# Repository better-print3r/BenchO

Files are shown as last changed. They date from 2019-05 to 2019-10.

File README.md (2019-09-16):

# BenchO

## A universal test standard for 3D printers.



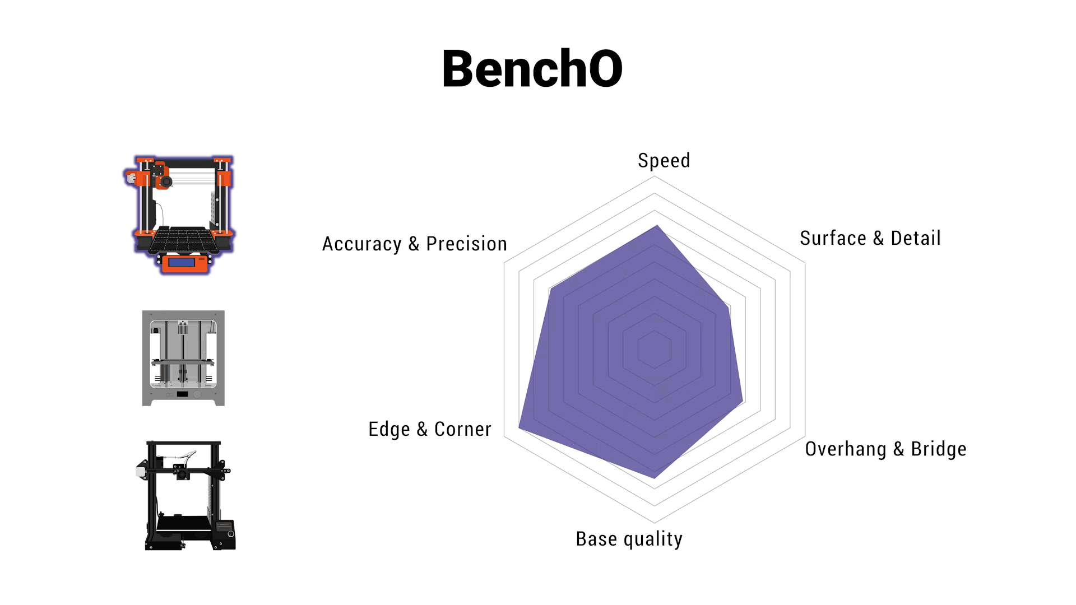
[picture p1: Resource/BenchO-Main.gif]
avatar

- #### Comprehensive
- #### Practical
- #### Professional 
## Aims of BenchO
- #### To test and compare the performance of various 3D printers
- #### To discuss and optimize profiles for different situation
- #### To calibrate and improve your printers
- #### To improve 3D printing experience for everyone
## Table of Contents
#### BenchO in a nutshell
- [What is BenchO?](#what-is-bencho)
- [Why we do this?](#why-we-do-this)
- [How do we achieve our goal?](#how-do-we-achieve-our-goal)
#### Test with BenchO
- [Preparation](#preparation)
- [Standard Test](#standard-fdm-test)
- [FAQs](#faqs)
- [Contributing](#contributing)
- [License](#license)
#### How to reach us
- [Contact infomation](#contact-infomation)

### What is BenchO?
BenchO is an open source project started by **Better Printer Institution LLC**.  Aiming to provide a universal test standard for the industry.  In our test, we provide specialized models and procedure to estimate the capability of your 3D printer.We will also provide optimized profile(in slicing software) for makers all over the world to suit thier needs. 

The current version contains protocols for consumer grade FDM printer. More test protocols will be added later in the future. The project is entirely open source.

In summary this is a place to **test, evaluate**,**discuss** and **improve** your 3D printer.

### Why we do this?

There are many 3D printers in the market and they are in all kinds of shapes and structures. For users it is really difficult to tell how much the difference really is between them.

How is the actual performance compare to what they advertised? Where is the limit of your printer? These questions are usually hard to find out.Besides that, even if you tried to find those answers, there is no such thing as a universal benchmark for you to discuss and compare with other machines. 

Thus we decide to make a universal, data based, open sourced project as you seen here. 

We believe that by making a universal standard for 3D printers, we could make this field better in the future.

### How do we achieve our goal?

In this project we currently provide a sufficient offline tool. This tool will allow 3D printer users get to know the capabilities of their machines and thus improve the performance of their printers. Our current test will be the starting point of BenchO.

## Standard FDM test

### Preparation for FDM 3D printer

- **eSUN PLA+ filament (Grey)** as standard test filament
- The 3D printer you want to test with
- A caliper with resolution up to 0.01mm and range larger than 100mm
- [BenchO Tool]() ([Offline version](Standard%20FDM%20test/BenchO_offline_ver20190902.xlsx))
- [Test Models](3Dmodel)

####
Check **[here](Standard%20FDM%20test)** to participate in BenchO test.

## FAQs
- **Q**: Why eSUN PLA+ with Grey color?
- **A**: eSUN filament is widely available all across the world. This makes BenchO testers having same material so the result is comparable. Grey is for checking surface details. We found this color be good to spot defects in your art print.
####
- **Q**:I saw the project is started by Better Printer Institution LLC. But why are you guys making profiles and improvements even for your competitors?
- **A**:Because we want a better community overall. Moderate competition and more cooperation will greatly improve the quality of 3D printing communities.This will eventually benefit us all,both users and companies.
## Maintainers

BenchO Team

## Contributing

See [the contributing file](CONTRIBUTING.md)!

Small note: If editing the Readme, please conform to the [standard-readme](https://github.com/RichardLitt/standard-readme) specification.

## License
This project is licensed under the Apache License, Version 2.0. See
[LICENSE](LICENSE)
## Contact Infomation
- The offical website:[http://foldy3d.com/](http://foldy3d.com/) 
- The Facebook Page:[https://www.facebook.com/BetterPrint3r/](https://www.facebook.com/BetterPrint3r/)

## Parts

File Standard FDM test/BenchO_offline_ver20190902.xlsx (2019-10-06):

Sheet: Basic
An Universal 3D printer test standard
Part1: Basic Precision
Section 1
Large Scale
No. | Value(mm) | Average(mm) | This part will reflect the relative precision and the absolute accuracy of your printer.The International Tolerance table reference ISO 286 has been applied here.
L1 | 99.71 | 99.55
L2 | 99.51
L3 | 99.52
L4 | 99.59 |  | For this section , all data should be enter in exact order.
L5 | 99.61
L6 | 99.47
L7 | 99.42
L8 | 99.54
 |  |  | Subject | Score | Hint:All good
 |  |  | XY relative precision | 5.48 out of 6
 |  |  | XY accuracy | 2 out of 4
 |  |  | Tolerance Grade | IT12
Section 2
Small Scale
No. | Value(mm) | Average(mm) | This part will reflect the absolute accuracy of your printer.The International Tolerance table reference ISO 286 has been applied here.
1 | 9.91 | 9.89
2 | 9.90
3 | 9.86
4 | 9.86 |  | In this section no specific data order is required.You should take data from different locations on model and fill all the blank.
5 | 9.89
6 | 9.87
7 | 9.93
8 | 9.93
9 | 9.89
10 | 9.86
Z axis
No. | Value(mm) | Average(mm) | Subject | Score | Grade | To see more details about grade, check Misc tab
1 | 100.22 | 100.27 | Small Scale accuracy | 2.8 out of 4 | IT11
2 | 100.25
3 | 100.29 |  | Z axis accuracy | 2.8 out of 4 | IT11
4 | 100.30
End of the section, please proceed to the next tab

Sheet: Engineering
BenchoO
An Universal 3D printer test standard
Part2: Engineering
Section 1
Base Quality
No. | Thickness(mm) | Average(mm) | Print Time |  | Hint:You must use your actual print time.
T1 | 9.86 | 9.94 | Hour | Min
T2 | 10.01 |  | 5 | 58
T3 | 9.77 |  | For this section , all data should be enter in exact order. This part measures the degree of parallel between base and surface.
T4 | 10.03
T5 | 9.87
T6 | 10.02
T7 | 9.80
T8 | 9.91
T9 | 10.21
Edge & Corner
No. | Thickness(mm) | Distortion(mm) | Score | Grade | This part measures the overshoot around corner.
V1 | 7.96 | 0.14 | 4.5 out of 5 | IT9
V2 | 7.91
V3 | 7.84
V4 | 7.94
V5 | 7.82
V6 | 7.83
Parallel
Feature |  | Status | Divergence(Deg) |  | Score(%) | 98.00%
Ueven X axi |  | No | 0.00955
Ueven Y axi |  | No | 0.01910
Flatness
Feature |  | Status | Score(%) | 46.00%
Uneven thickness |  | Yes
Convex |  | Yes
Section 2
Curvature
 | Bending Distance(mm)
No. | X axi
1 | 0.20
2 | 0.20
3 | 0.02
4 | 0.20
No. | Y axi
1 | 0.10
2 | 0.10
3 | 0.10
4 | 0.00
Concave Down？ |  | No
Direction |  | Radius | Score |  | The radius here refer to the circle you need if you use your base as an arc.
X axi |  | 32258.10 | 100.00%
Y axi |  | 30826.69 | 100.00%
Summary
Condition |  | Sub Total(%) | Overall(%) | Score | Hint: Even one small drawbacks can lower your score significantly
Parallel |  | 98.00% | 45.00% | 4.5 out of 10
Flatness |  | 46.00%
Curvature |  | 100.00%
Section 3
Print Time |  | Hour | Min | Hint:You must use your actual print time.
 |  | 2 | 0
Large Holes
No. | Inner(mm) | Average(mm) | Under size? |  | Hint:Precision indicates how homogeneous your circle is. While Accuracy shows how much your circle deviates from design
1 | 79.86 | 79.86 | Yes
2 | 79.87 |  | Off Set(mm)
3 | 79.82 |  | -0.18
4 | 79.91 |  | Score(%) |  | Grade | Score
5 | 79.84 |  | Precision | 60.00% | 9 | 1.3 out of 2.5
6 | 79.88 |  | Accuracy | 40.00% | IT10
Large Shafts
No. | Outer(mm) | Average(mm) | Over size? |  | Hint:Here the precision uses chart ISO 286-2,while accuracy uses chart ISO 286. To see details please check Misc tab
1 | 99.92 | 99.93 | No
2 | 99.96 |  | Off Set(mm)
3 | 99.95 |  | -0.11
4 | 99.89 |  | Score(%) |  | Grade | Score
5 | 99.90 |  | Precision | 70.00% | 8 | 1.95 out of 2.5
6 | 99.97 |  | Accuracy | 90.00% | IT9
Small Holes
No. | Inner(mm) | Average(mm) | Under size? |  | If your printer score badly this part. Dont worry. Most printers wont score over 50%
1 | 29.93 | 29.93 | Yes
2 | 29.95 |  | Off Set(mm)
3 | 29.92 |  | -0.13
4 | 29.87 |  | Score(%) |  | Grade | Score
5 | 29.93 |  | Precision | 40.00% | 10 | 1 out of 2.5
6 | 29.97 |  | Accuracy | 40.00% | IT10
Small Shafts
No. | Outer(mm) | Average(mm) | Over size? |  | Only when a hole is not under size and a shaft is not over size. It can be granted H/h grade
1 | 49.98 | 49.94 | No
2 | 49.91 |  | Off Set(mm)
3 | 49.96 |  | -0.09
4 | 49.92 |  | Score(%) |  | Grade | Score
5 | 49.94 |  | Precision | 60.00% | 9 | 1.8 out of 2.5
6 | 49.95 |  | Accuracy | 90.00% | IT9
End of the section, please proceed to the next tab

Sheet: Art
BenchoO
An Universal 3D printer test standard
Part3: Art
Section 1
Art1
Print Time |  | Hour | Min | Hint:You must use your actual print time.
 |  | 1 | 8
Subject | Condition | Score
Overhang Level | 4 | 4 out of 4
cameo level | 3 | 2.4 out of 4
Ringing size(Included) | 4mm | 3.5 out of 5
Art2
Print Time |  | Hour | Min | Hint:You must use your actual print time.
 |  | 0 | 49
Subject | Condition | Score
Clear space between bridge | Yes | 1 out of 1
Bridge to bottom Distance(mm) | 11.42 | 2.86 out of 3
Stringing | Clean | 3 out of 3
Full hieght | Yes | 1 out of 1
Disk(Minimum layer height) | 0.05mm | 2.8 out of 4
Sum | 20.56 out of 25
End of the Test. Please check Result Tab for detailed summary

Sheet: Result
BenchoO
An Universal 3D printer test standard
Result
Basic Precision
Subject | Score | Score(%) | Sum |  | Score | Score(%)
XY relative precision | 3.66 out of 4 | 91.40% |  |  | 13.08 out of 18 | 72.69%
XY accuracy | 3 out of 6 | 50.00%
Small Scale accuracy | 2.8 out of 4 | 70.00%
Z axis accuracy | 2.8 out of 4 | 70.00%
Engineering
Subject | sub Score(%) | Sub total(%) | Sub Score | Sum | Score | Score(%)
Surface Flatness | 46.00% | 45.00% | 4.5 out of 10 |  | 15.05 out of 25 | 60.20%
Surface Parallel | 98.00%
Surface Curvature | 100.00%
Subject | Score | Score(%)
Vertical Distortion | 4.5 out of 5 | 90.00%
Shafts | 3.75 out of 5 | 75.00%
Holes | 2.3 out of 5 | 46.00%
Art
Surface condition |  |  |  | Sum | Score | Score(%)
 |  |  | Sub Sum |  | 20.56 out of 25 | 82.24%
Stringing | 3 out of 3 | 100.00% | 6.5 out of 8
Ringing | 3.5 out of 5 | 70.00%
Fine detail
Subject | Score | Score(%) | Sub Sum
Camo Level | 2.4 out of 4 | 60.00% | 6.2 out of 9
Spike Height | 1 out of 1 | 100.00%
Disk feature | 2.8 out of 4 | 70.00%
Overhang & Bridge
Subject | Score | Score(%) | Sub Sum
Overhang | 4 out of 4 | 100.00% | 7.86 out of 8
Bridge Height | 2.86 out of 3 | 95.33%
Clear space between Bridge | 1 out of 1 | 100.00%
Time
Part | Score | Score(%) | Sum |  | Score | Score(%)
Engineering1 | 9.099 out of 10 | 90.99% |  |  | 30.71 out of 32 | 95.97%
Engineering2 | 6 out of 6 | 100.00%
Art1 | 10 out of 10 | 100.00%
Art2 | 5.612 out of 6 | 93.53%
Overall Sum
Subject | Score | Score(%) | Sum |  | Score | Score(%)
Basic Precision | 12.26 out of 18 | 68.11% |  |  | 78.58 out of 100 | 78.58%
Engineering | 15.05 out of 25 | 60.20%
Art | 20.56 out of 25 | 82.24%
Time | 30.71 out of 32 | 95.97%
End of the Test

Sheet: Process
No. | Basicdiff | Absdiff | relative | No. | smalldiff | Zdiff | s accuracy | No. | H diff | absHdiff | X div | Para score | radius x | Xscore |  | Art | Surface Condition | 81.25% | 6.50 | Max Time
1 | -0.29 | 0.29 | 0.91 | 1 | -0.09 | 0.22 | 0.70 | 1 | -0.14 | 0.14 | 0.00955 | 0.98 | 32258.10327 | 1 | hang | 4.00 | Fine Details | 68.89% | 6.20 | Part | ENG1 | ENG2 | ART1 | ART2
2 | -0.49 | 0.49 | accuracy | 2 | -0.10 | 0.25 | s grade | 2 | 0.01 | 0.01 | Y div | Flat score | radius Y | Yscore | cam | 2.40 | Bridge&Overhang | 98.25% | 7.86 | Time | 362.00 | 182.00 | 90.00 | 51.00
3 | -0.48 | 0.48 | 0.50 | 3 | -0.14 | 0.29 | IT11 | 3 | -0.23 | 0.23 | 0.0191 | 0.46 | 30826.68542 | 1 | ring | 3.50 |  |  |  | Max time | 724.00 | 364.00 | 180.00 | 102.00
4 | -0.41 | 0.41 | Grade | 4 | -0.14 | 0.30 |  | 4 | 0.03 | 0.03 | UnevenX | Hint1 |  |  | space | 1.00 |  |  |  | Time Step | 4.02222 | 2.02222 | 1.00000 | 0.56667
5 | -0.39 | 0.39 | IT12 | 5 | -0.11 |  |  | 5 | -0.13 | 0.13 | No | Your base is parallel |  |  | bridge | 2.86 |  |  |  | Cur Time | 358.00 | 120.00 | 68.00 | 49.00
6 | -0.53 | 0.53 | XY mean | 6 | -0.13 |  |  | 6 | 0.02 | 0.02 | UnevenY | Hint2 |  |  | str | 3.00 | Basic Precision | 68.11% | 12.26 | R Score | 90.99% | 120.66% | 112.00% | 93.53%
7 | -0.58 | 0.58 | 99.56 | 7 | -0.07 |  |  | 7 | -0.20 | 0.20 | No | Your Base is thicker in the center |  |  | Height | 1.00 | Engineering | 60.20% | 15.05 | Score | 0.91 | 1.00 | 1.00 | 0.94
8 | -0.46 | 0.46 | misaline | 8 | -0.07 |  |  | 8 | -0.09 | 0.09 | convex | Hint3 |  |  | disk | 2.80 | Art | 82.24% | 20.56 | F Score | 9.10 | 6.00 | 10.00 | 5.61
 | Reldiff | absrel | No | No. | s.absdiff | sabszdiff | z accuracy |  | V diff |  | Yes |  |  |  |  |  | Time | 95.97% | 30.711
1 | 0.14 | 0.14 | Hint | 1 | 0.09 | 0.22 | 0.70 |  | 0.14 |  | uneven thick | Sum score
2 | -0.05 | 0.05 | All good | 2 | 0.10 | 0.25 | z grade |  |  |  | Yes | 0.45 |  |  |  |  | Engineering1 | 90.99%
3 | -0.05 | 0.05 |  | 3 | 0.14 | 0.29 | IT11 |  |  |  | Vscore |  |  |  |  |  | Engineering2 | 100.00%
4 | 0.03 | 0.03 |  | 4 | 0.14 | 0.30 |  |  |  |  | 0.9 |  |  |  |  |  | Art1 | 100.00%
5 | 0.05 | 0.05 |  | 5 | 0.11 |  |  |  |  |  | Vgrade |  |  |  |  |  | Art2 | 93.53%
6 | -0.09 | 0.09 |  | 6 | 0.13 |  |  |  |  |  | IT9
7 | -0.14 | 0.14 |  | 7 | 0.07
8 | -0.02 | 0.02 |  | 8 | 0.07
No. | LHdiff | LH pre | off | No. | LSdiff | LS pre | off | No. | SHdiff | SH pre | off | Surface Flatness |  | 46.00%
1 | 0.04 | 0.60 | -0.18 | 1 | 0.05 | 0.70 | -0.11 | 1 | 0.06 | 0.40 | -0.13 | Surface Parallel |  | 98.00%
2 | 0.05 | LH grade | Max diff | 2 | 0.01 | LS grade | Max diff | 2 | 0.08 | SH grade | Mindiff | Surface Curvature |  | 100.00%
3 | 0.00 | 9 | 0.18 | 3 | 0.02 | 8 | 0.11 | 3 | 0.05 | 10 | 0.13 | Vertical Distortion |  | 90.00%
4 | 0.09 | Under | LH acc | 4 | 0.08 | Over | LS acc | 4 | 0.00 | Under | SH acc | Shafts |  | 75.00%
5 | 0.02 | Yes | 0.4 | 5 | 0.07 | No | 0.9 | 5 | 0.06 | Yes | 0.40 | Holes |  | 46.00%
6 | 0.06 | acc grade | IT10 | 6 | 0.00 | acc grade | IT9 | 6 | 0.10 | acc grade | IT10
No. | ABS diff |  |  | No. | ABS diff |  |  | No. | ABS diff
1 | 0.14 |  |  | 1 | 0.08 |  |  | 1 | 0.07
2 | 0.13 |  |  | 2 | 0.04 |  |  | 2 | 0.05
3 | 0.18 |  |  | 3 | 0.05 |  |  | 3 | 0.08
4 | 0.09 |  |  | 4 | 0.11 |  |  | 4 | 0.13
5 | 0.16 |  |  | 5 | 0.10 |  |  | 5 | 0.07
6 | 0.12 |  |  | 6 | 0.03 |  |  | 6 | 0.03
No. | SSdiff | SS pre | off
1 | 0.00 | 0.60 | -0.09
2 | 0.07 | SS grade | Maxdiff
3 | 0.02 | 9 | 0.09
4 | 0.06 | Over | SS acc
5 | 0.04 | No | 0.9
6 | 0.03 | acc grade | IT9
No. | ABS diff
1 | 0.02 | Shafts | Holes
2 | 0.09 | 0.75 | 0.46
3 | 0.04
4 | 0.08
5 | 0.06
6 | 0.05

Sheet: Misc
Space |  | Cameo level |  | Stringing level |  | Spikes |  | Disk |  | Fail |  | Over/Under Size |  | Overhang |  | Ringing level
Yes | 1 | level | Score | Condition | Score | Height | Score | Height | Score | Yes | 0 | Yes | 0.5 | Height | Score | Condition | Score
Some | 0.3 | 0 | 0.00 | Clean | 1.00 | Full | 1.00 | 0.025mm | 1.00 | No | 1 | No | 1 | 4 | 1.00 | 2mm | 1.00
No | 0 | 1 | 0.20 | Ok | 0.60 | Most | 0.70 | 0.05mm | 0.70 | Full Height |  | Uneven |  | 3 | 0.75 | 4mm | 0.70
 |  | 2 | 0.40 | Bad | 0.20 | Some | 0.50 | 0.1mm | 0.50 | Yes | 1 | Yes | 0.5 | 2 | 0.50 | 8mm | 0.50
 |  | 3 | 0.60 | Fail | 0.00 | Nope | 0.00 | Fail | 0.00 | No | 0 | No | 1 | 1 | 0.25 | Fail | 0.00
 |  | 4 | 0.80 |  |  |  |  |  |  |  |  |  |  | 0 | 0.00
 |  | 5 | 1.00
Tolorence table |  |  |  |  |  |  | Max Time
Grade | Tolerance100(mm) | Tolerance10(mm) | Tolerance30(mm) | Tolerance50(mm) | Tolerance80(mm) | Score | Part | ENG1 | ENG2 | ART1 | ART2
Perfect | 0.000 | 0.000 | 0.000 | 0.000 | 0.000 | 1.00 | time(min) | 362 | 182 | 90 | 51
IT8 | 0.054 | 0.022 | 0.033 | 0.039 | 0.046 | 1.00
IT9 | 0.087 | 0.036 | 0.052 | 0.062 | 0.074 | 0.90
IT10 | 0.140 | 0.058 | 0.084 | 0.100 | 0.120 | 0.80
IT11 | 0.220 | 0.090 | 0.130 | 0.160 | 0.190 | 0.70
IT12 | 0.350 | 0.150 | 0.210 | 0.250 | 0.300 | 0.60
IT13 | 0.540 | 0.220 | 0.330 | 0.390 | 0.460 | 0.50
IT14 | 0.870 | 0.360 | 0.520 | 0.620 | 0.740 | 0.40
IT15 | 1.400 | 0.580 | 0.840 | 1.000 | 1.200 | 0.30
IT16 | 2.200 | 0.900 | 1.300 | 1.600 | 1.900 | 0.10
Reject | 3.000 | 3.000 | 3.000 | 3.000 | 3.000 | 0.00
TimeScore |  |  |  |  |  | Surface Smoothness |  | Shafts |  |  |  |  | Holes
Ulti | 0.86 | Ender3 | 0.72 |  |  | Condition | Score | Grade | (30mm,50mm] | (50mm,80mm] | (80mm,120mm] | Score | Grade | <=30 | <=50 | <=80 | <=120 | Score
Prusa | 0.8 |  |  |  |  | Good | 1.00 | Perfect | 0.000 | 0.000 | 0.000 | 1.00 | Perfect | 0.000 | 0.000 | 0.000 | 0.000 | 1.00
Cr10s | 0.81 |  |  |  |  | Decent | 0.80 | 5 | 0.011 | 0.001 | 0.015 | 1.00 | 6 | 0.013 | 0.016 | 0.019 | 0.022 | 1.00
 |  |  |  |  |  | Bad | 0.50 | 6 | 0.016 | 0.019 | 0.022 | 0.90 | 7 | 0.021 | 0.025 | 0.030 | 0.035 | 0.90
 |  |  |  |  |  | Fail | 0.00 | 7 | 0.025 | 0.030 | 0.035 | 0.80 | 8 | 0.033 | 0.039 | 0.046 | 0.054 | 0.8
 |  |  |  |  |  |  |  | 8 | 0.039 | 0.046 | 0.054 | 0.70 | 9 | 0.052 | 0.062 | 0.074 | 0.087 | 0.6
 |  |  |  |  |  |  |  | 9 | 0.062 | 0.074 | 0.087 | 0.60 | 10 | 0.084 | 0.1 | 0.12 | 0.14 | 0.4
 |  |  |  |  |  |  |  | 10 | 0.100 | 0.120 | 0.140 | 0.50 | 11 | 0.13 | 0.16 | 0.19 | 0.22 | 0.2
 |  |  |  |  |  |  |  | 11 | 0.160 | 0.190 | 0.220 | 0.30 | Reject | 1.00 | 1.00 | 1.00 | 1.00 | 0.00
 |  |  |  |  |  |  |  | 12 | 0.250 | 0.300 | 0.350 | 0.10
 |  |  |  |  |  |  |  | Reject | 1.000 | 1.000 | 1.000 | 0.00

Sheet: Score Weight
BenchoO
An Universal 3D printer test standard
Score Distribution
section | subsection | Weight | Subtotal
Part1: Basic Precision | XY relative precision | 6 | 18
 | XY accuracy | 4
 | Small Scale accuracy | 4
 | Z axis accuracy | 4
Part2: Engineering | Base Quality | 10 | 25
 | Edge and corner | 5
 | Large Holes | 2.5
 | Large Shafts | 2.5
 | Small Holes | 2.5
 | Small Shafts | 2.5
Part3: Art | Overhang Level | 4 | 25
 | cameo level | 4
 | Ringing size(Included) | 5
 | Clear space between bridge | 1
 | Bridge to bottom Distance(mm) | 3
 | Stringing | 3
 | Full height | 1
 | Disk(Minimum layer height) | 4
Part4:Time | Engineering1 | 10 | 32
 | Engineering2 | 6
 | Art1 | 10
 | Art2 | 6
Total | 100

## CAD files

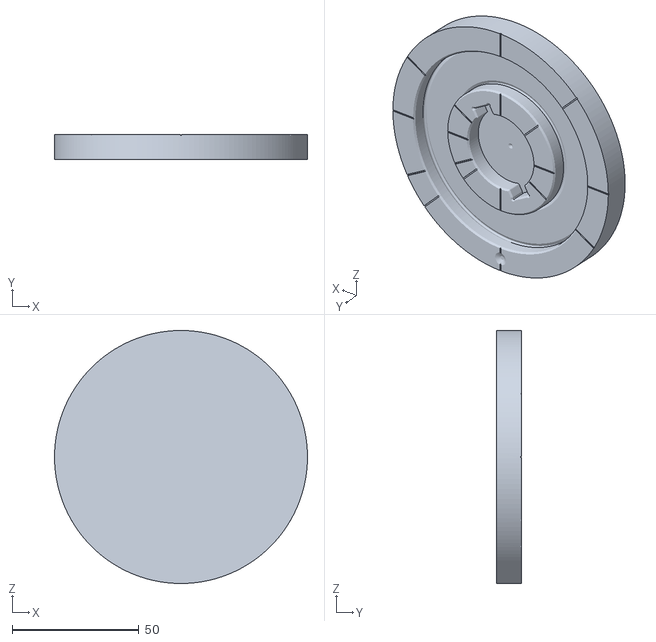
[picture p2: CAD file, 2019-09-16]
3Dmodel/Engineering2.STL
100.0 x 10.0 x 100.0

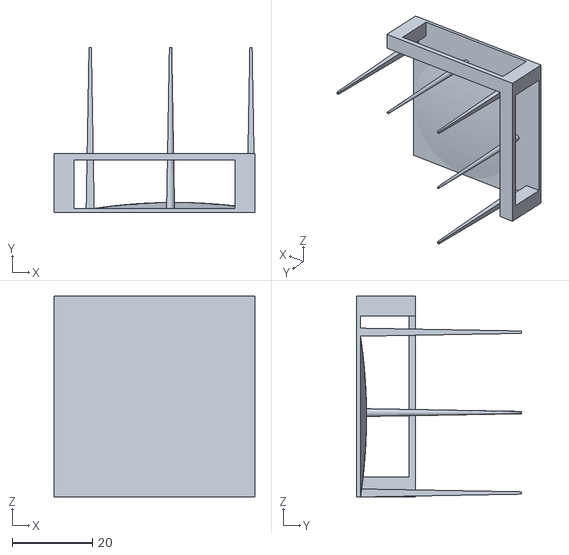
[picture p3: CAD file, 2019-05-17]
Test Models/Art_2.STL
50.0 x 41.0 x 50.0

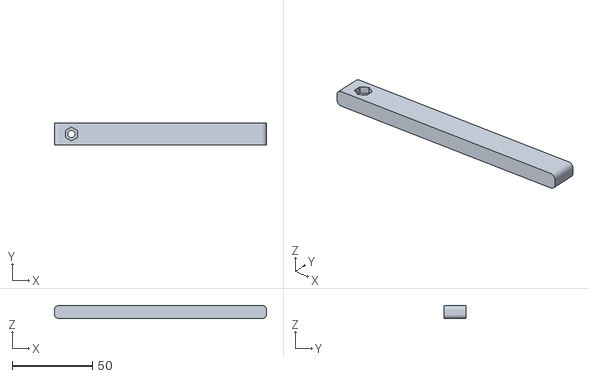
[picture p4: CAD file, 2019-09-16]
3Dmodel/Ruler.STL
132.0 x 14.0 x 8.00

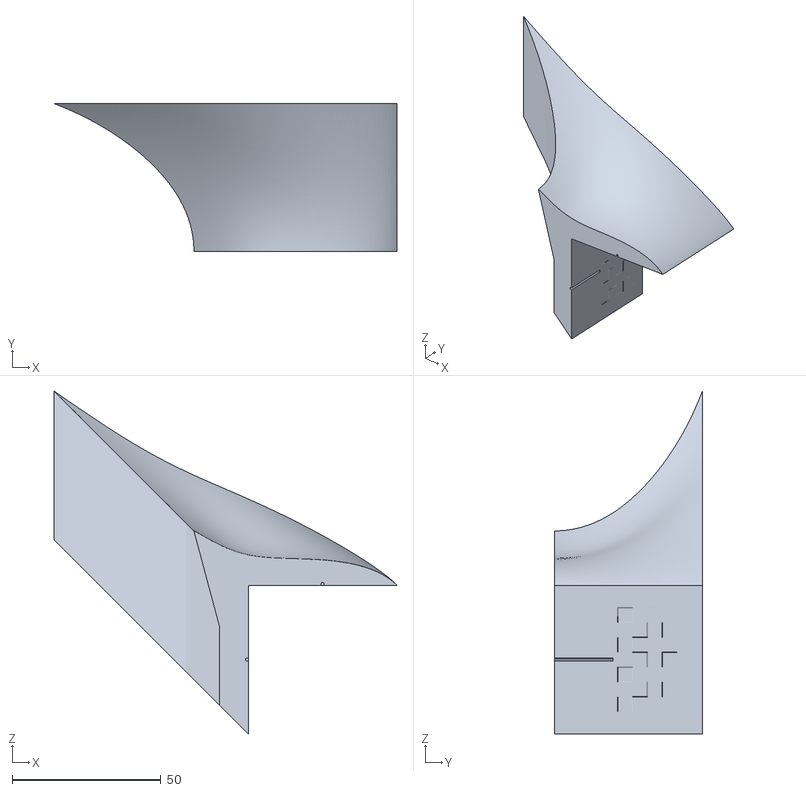
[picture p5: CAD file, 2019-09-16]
3Dmodel/Art1.STL
115.4 x 49.7 x 115.4

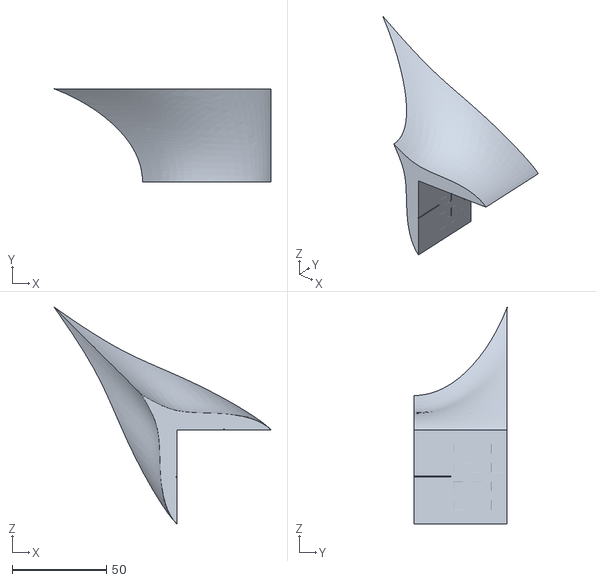
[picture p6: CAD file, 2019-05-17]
Test Models/Art_1.STL
115.4 x 49.7 x 115.4

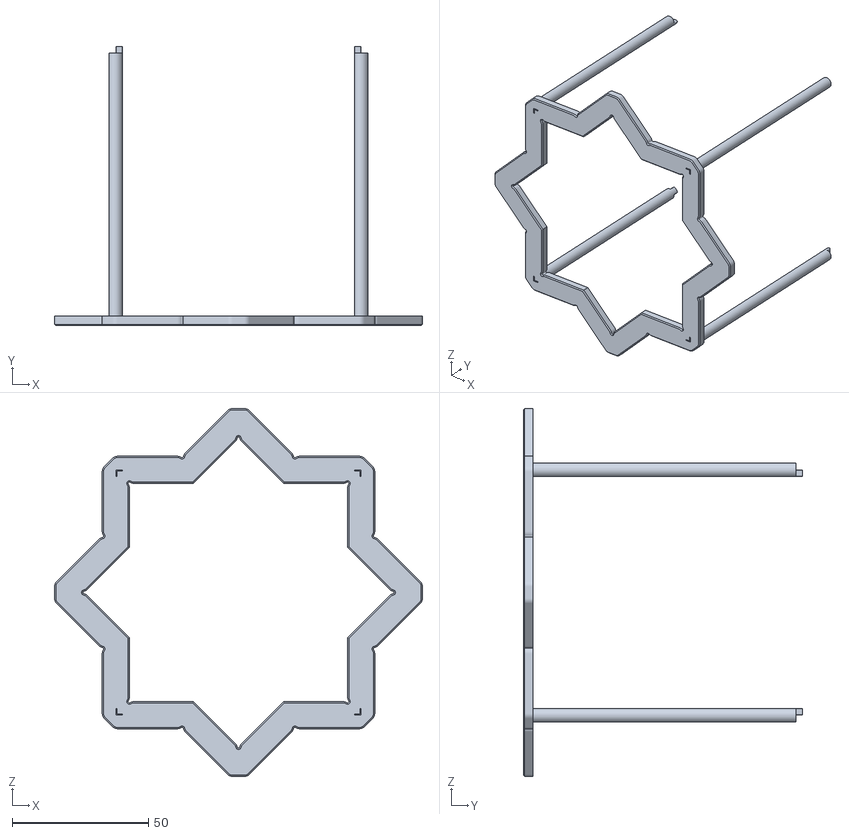
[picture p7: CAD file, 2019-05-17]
3Dmodel/Basic.STL
135.0 x 102.5 x 135.0

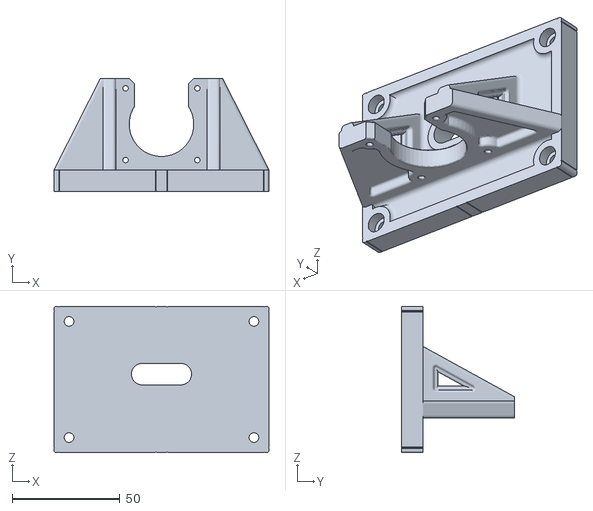
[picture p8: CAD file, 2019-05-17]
3Dmodel/Engineering1.STL
100.0 x 52.5 x 68.0

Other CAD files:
Test Models/Engineering_2.STL
3Dmodel/Art2.STL

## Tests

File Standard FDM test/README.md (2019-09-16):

Standard desktop FDM test
===============================

# Table of Contents
## STEP 1.Preparation & Info
- [Preparation](#step-1preparation)
- [General Info](#general-info)
## STEP 2.Test Model print & Settings
- [Basic Precision](#basic-precision)
- [Engineering](#engineering)
- [Art](#art)
- [Ruler](#ruler)
- [Tools](#tools)
## STEP 3.Measurement & Results
- [Precision & Accuracy](#precision--accuracy)
- [Base Quality & Edge](#base-quality--edge)
- [Base Bending](#base-bending)
- [Tolerance & Fit](#tolerance--fit)
- [Surface & Details](#surface--details)
- [Overhang & Bridge](#overhang--bridge)

## Test Example
- [Example](#example)
## FAQs
- [FAQs](#faqs)
## Score Distribution
- [Distribution table](#score-weight)
# STEP 1.Preparation

For Offline pdf version, Check [here](/Standard%20FDM%20test/BenchODocument.pdf).

## Software 
- **[BenchO]() ([Offline version](/Standard%20FDM%20test/BenchO_offline_ver20190823.xlsx))**
- [Test Models](/3Dmodel)
- [Tool Models(Ruler)](/3Dmodel/Ruler.STL)
## Hardware
- 3D printer for test
- **eSUN PLA+ filament(Grey)**
- A caliper with resolution up to 0.01mm and range larger than 100mm

# General Info

In the following section we will specify the parameters for standard test. You should print 5 test models in total to perform a complete test. In addition if you do not have a ruler(tool model) you should also print a ruler.
In our official test, all data are collected with **eSUN PLA+ (Grey)** .This type of filament should be widely available and easy to purchase. The Grey color makes it easier to identify surface details in the following test. If you use other types of filament. The result will be less comparable and will **not** be accept for official ranking.

This standard is created for desktop FDM 3D printers. Using this on other types of printer will generate inconclusive results.

# STEP 2.Test Model print & Settings
All models should strictly follow the designated parameters in a standard test.

**DO NOT RESCALE OR CHANGE THE TEST MODEL**.

You should start with a **default profile** in your slicing software and then change the parameters specified in the following section. For the parameters undeclared in the following section, keep it default.

Turn on all possible settings in your slicer. If you cannot find the settings required. Then it must be hidden in some advance menu in your slicing software.

**Do not** rotate the model along Z Axis in your slicing software
## Basic precision

There is only one model in this section: [Basic.stl](/3Dmodel/Basic.STL)

Using any default profile will be sufficient. You do not have to modify anything in specific but you could try different layer height.

## Engineering

There are two models: [Engineering1.stl](/3Dmodel/Engineering1.STL) and [Engineering2.stl](/3Dmodel/Engineering2.STL)

### Engineering1.stl
| Setting | Parameter |
|:---:|:---:|
| Layer height  | 0.2mm |
| Wall line count | 2 |
|  Infill density | 100% |
|  Infill pattern | line |
| Support | None |

### Engineering2.stl
| Setting | Parameter |
|:---:|:---:|
| Layer height  | 0.2mm |
| Wall line count | 2 |
|  Infill density | 66% |
|  Infill pattern | Triangles |
| Top layers | 0 |
|  Bottom layers  | 0 |
| Support | None |

## Art

There are two models: [Art1.stl](/3Dmodel/Art1.STL) and [Art2.stl](/3Dmodel/Art2.STL)

### Art1
| Setting | Parameter |
|:---:|:---:|
| Layer height  | 0.2mm |
| Wall line count | 3 |
|  Infill density | 0% |
| Top layers | 0 |
| Support | None |

### Art2
| Setting | Parameter |
|:---:|:---:|
| Layer height  | 0.2mm |
| Wall line count | 2 |
|  Infill density | 20% |
| Support | None |

### Ruler

There are one model:[Ruler.stl](/3Dmodel/Ruler.STL)

| Setting | Parameter |
|:---:|:---:|
| Layer height  | 0.2mm |
| Wall line count | 2 |
|  Infill density | 20% |
| Support | None |

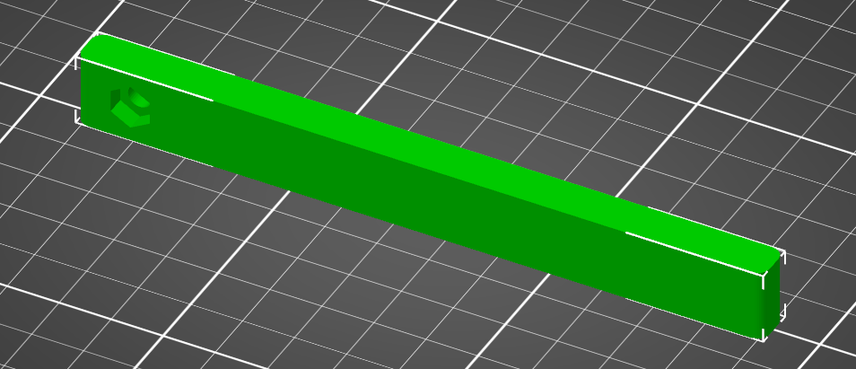
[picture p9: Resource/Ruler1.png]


When printing this part you should put the ruler along one of the axis

## Tools

A caliper with resolution not less than 0.01mm and range larger than 100mm will be sufficient for the measurement. All data should be taken in .

The printed ruler in previous section will be your additional tool.

Check your ruler with known straight edge.

# STEP 3.Measurement & Results

## Precision & Accuracy
During measurement you should ignore the defects that are easy to remove. The test is designed to reflect the capability of your printer.
####

<center class="half">
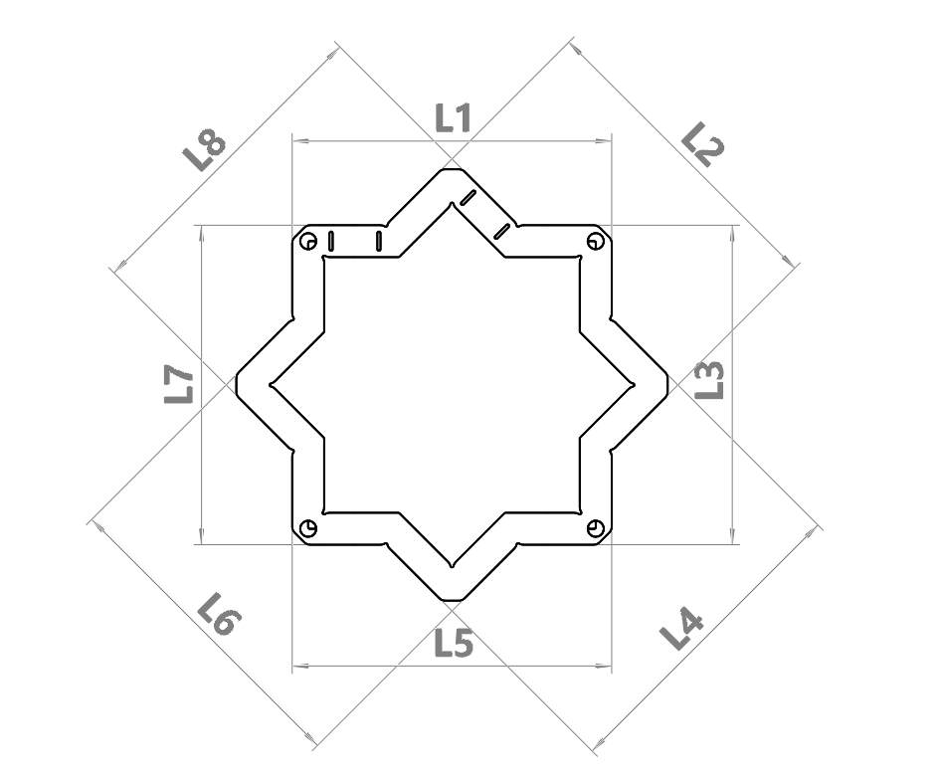
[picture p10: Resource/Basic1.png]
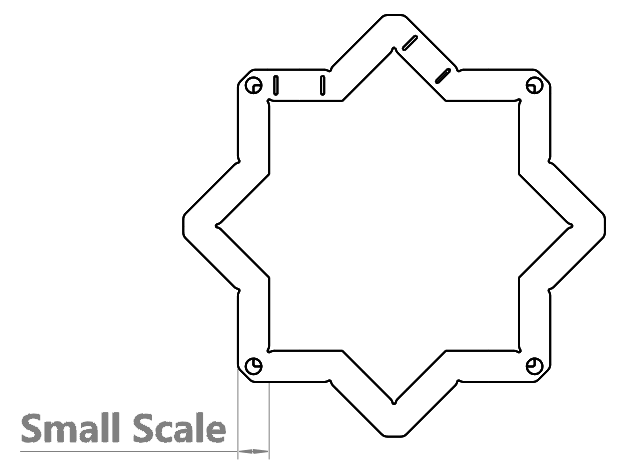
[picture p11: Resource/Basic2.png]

</center>

This is the top view of the test model.You should take 8 measurements and fill the associative blank.
####
avatar

This is the top view of the test model.You should take 10 measurements and fill the associative blank.In this part you do not have to take data by order.
####
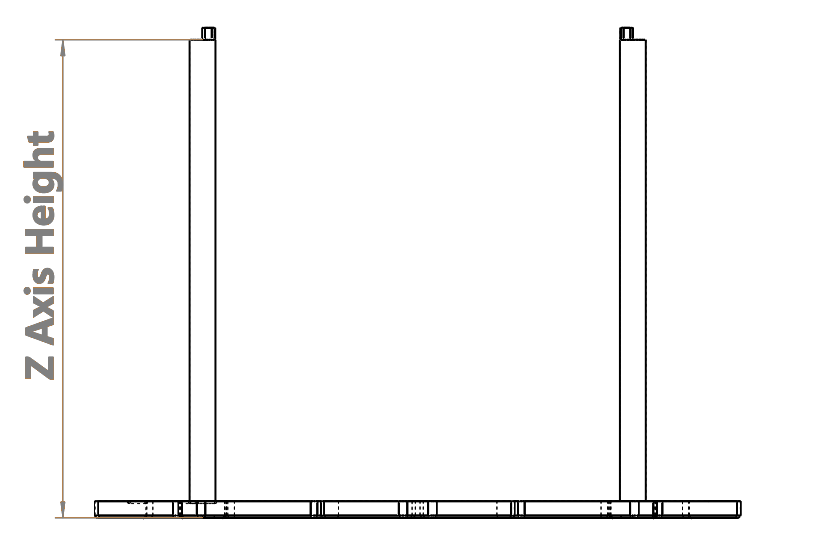
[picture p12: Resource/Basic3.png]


This is the front view of the test model.You should take 4 measurements and fill the associative blank.In this part you do not have to take data by order.

## Base Quality & Edge

####

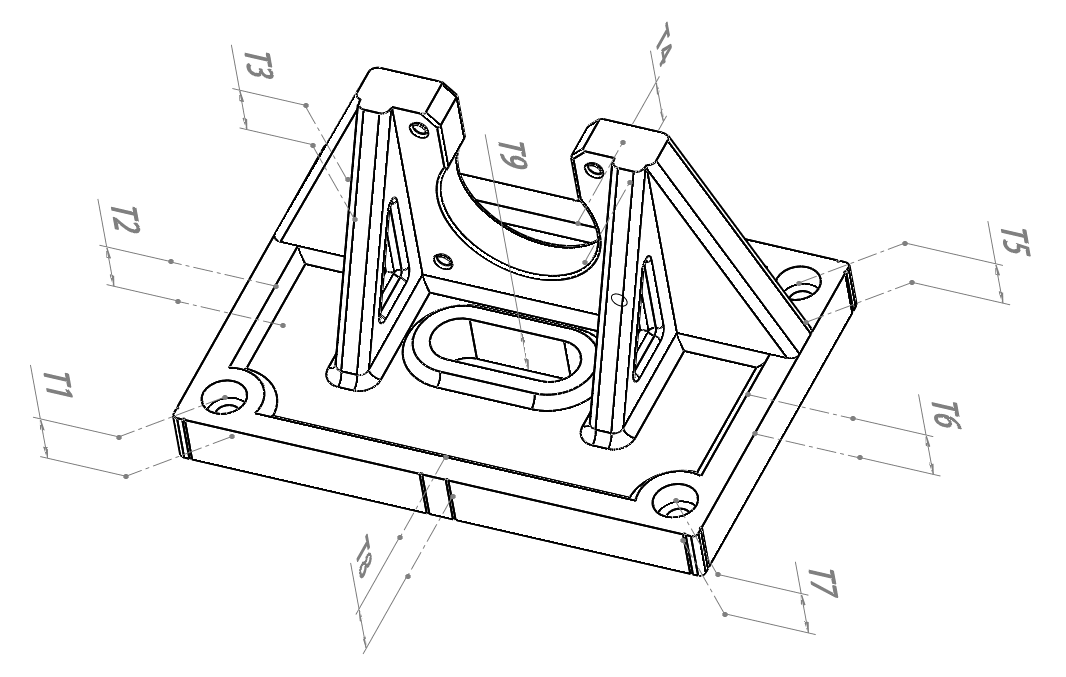
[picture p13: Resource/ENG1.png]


You should take 8 measurements and fill the associative blank.

####
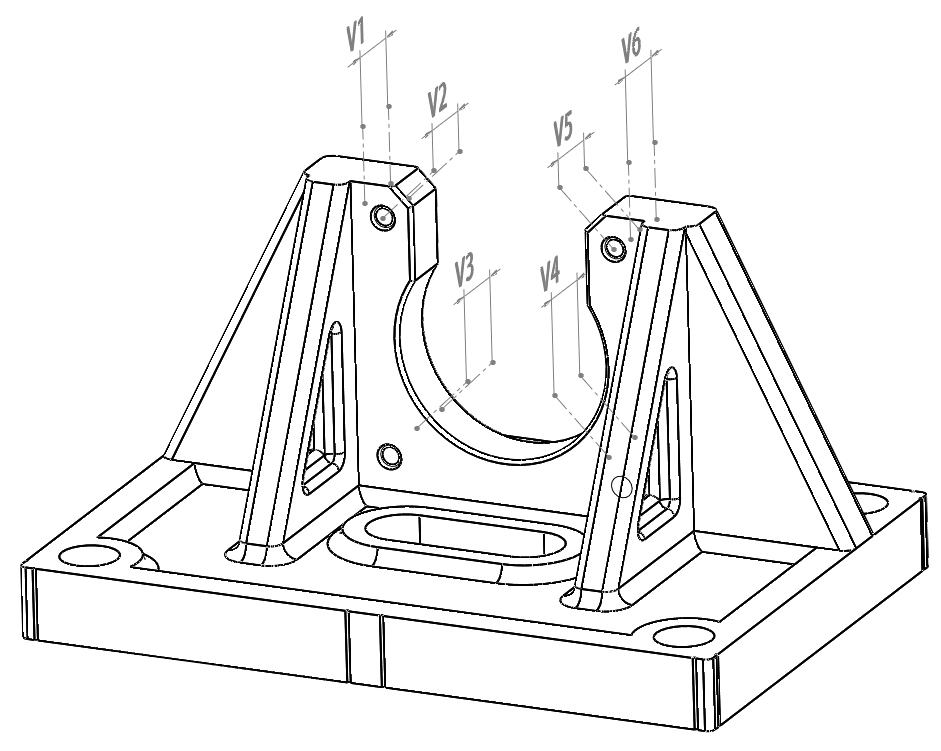
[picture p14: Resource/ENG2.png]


You should take 6 measurements and fill the associative blank.

## Base Bending

You should first bolt or fix your ruler in one of the four corner and then measure the gap between your ruler and the opposite side of the base. If there is no gap at all. Your result will be 0mm.
####

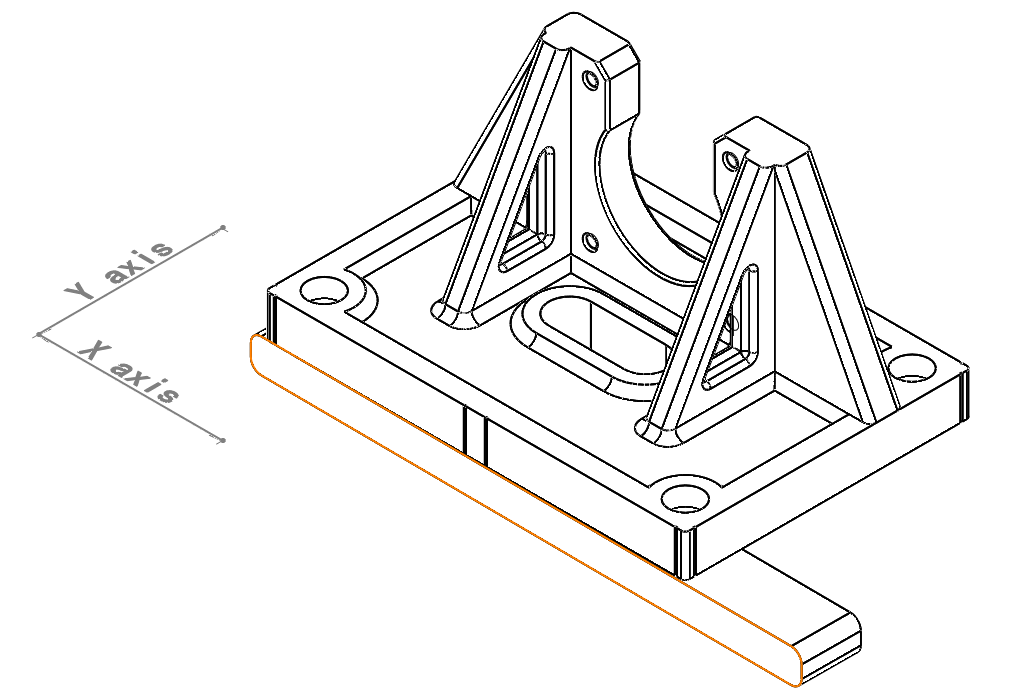
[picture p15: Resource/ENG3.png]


This will be an example for X axis measure.

####
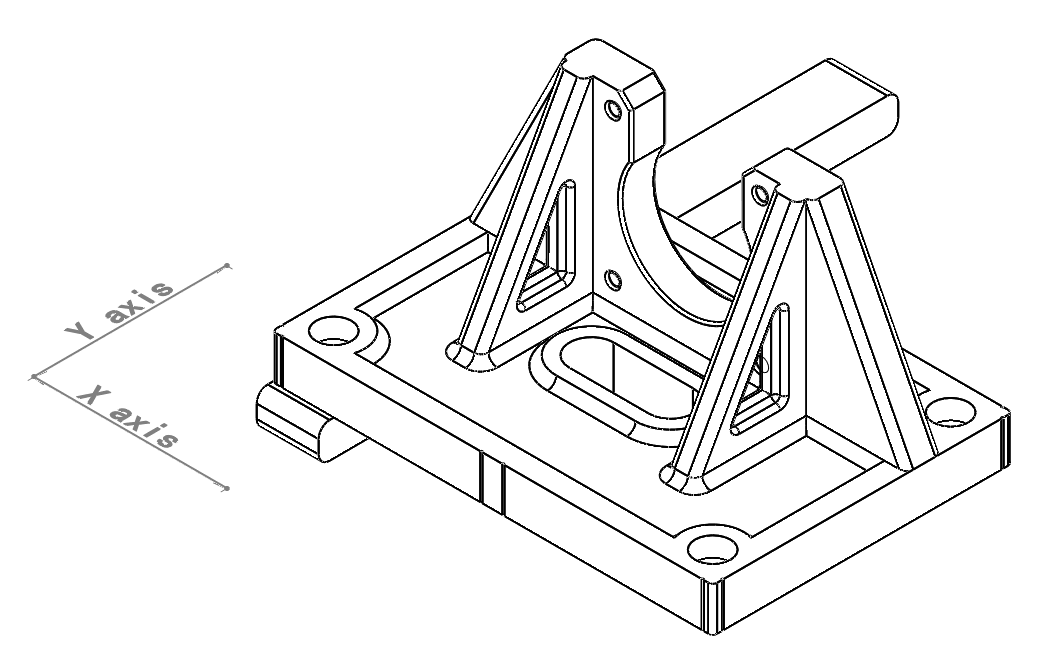
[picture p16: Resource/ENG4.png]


This will be an example for Y axis measure.

## Tolerance & Fit

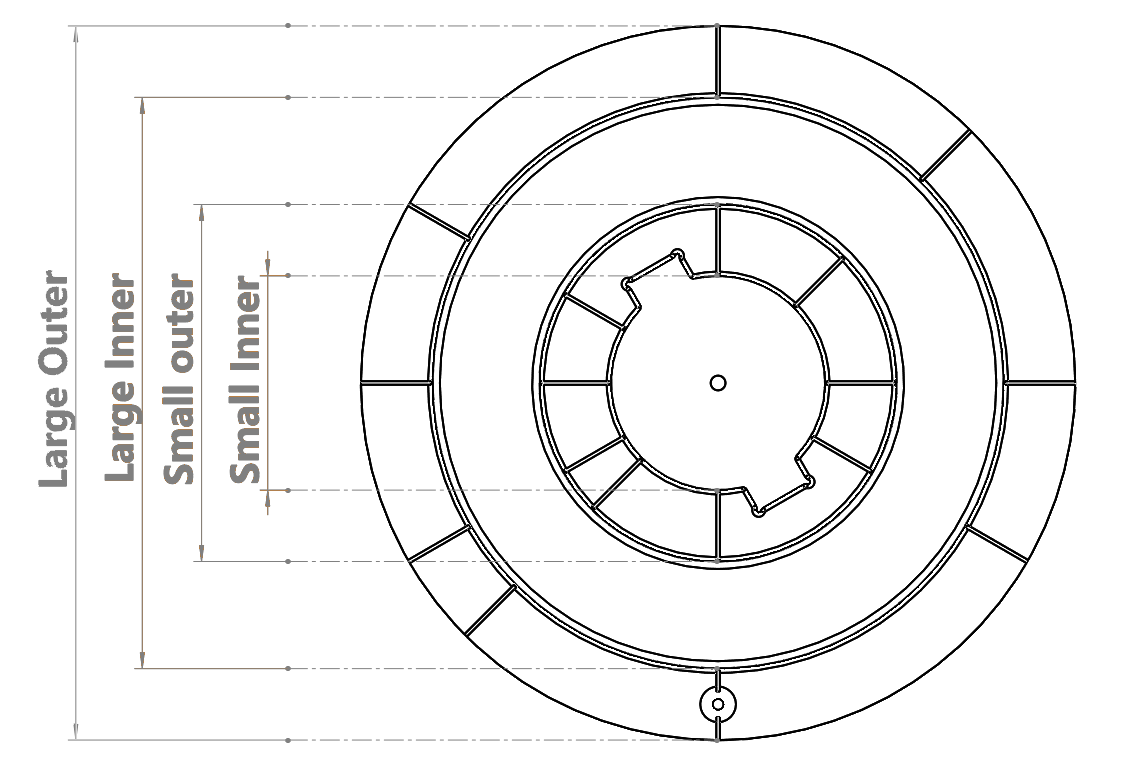
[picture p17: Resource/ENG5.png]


This is the Top view of the test model.You should take 6 measurements for each dimension and fill the associative blank

## Surface & Details

####
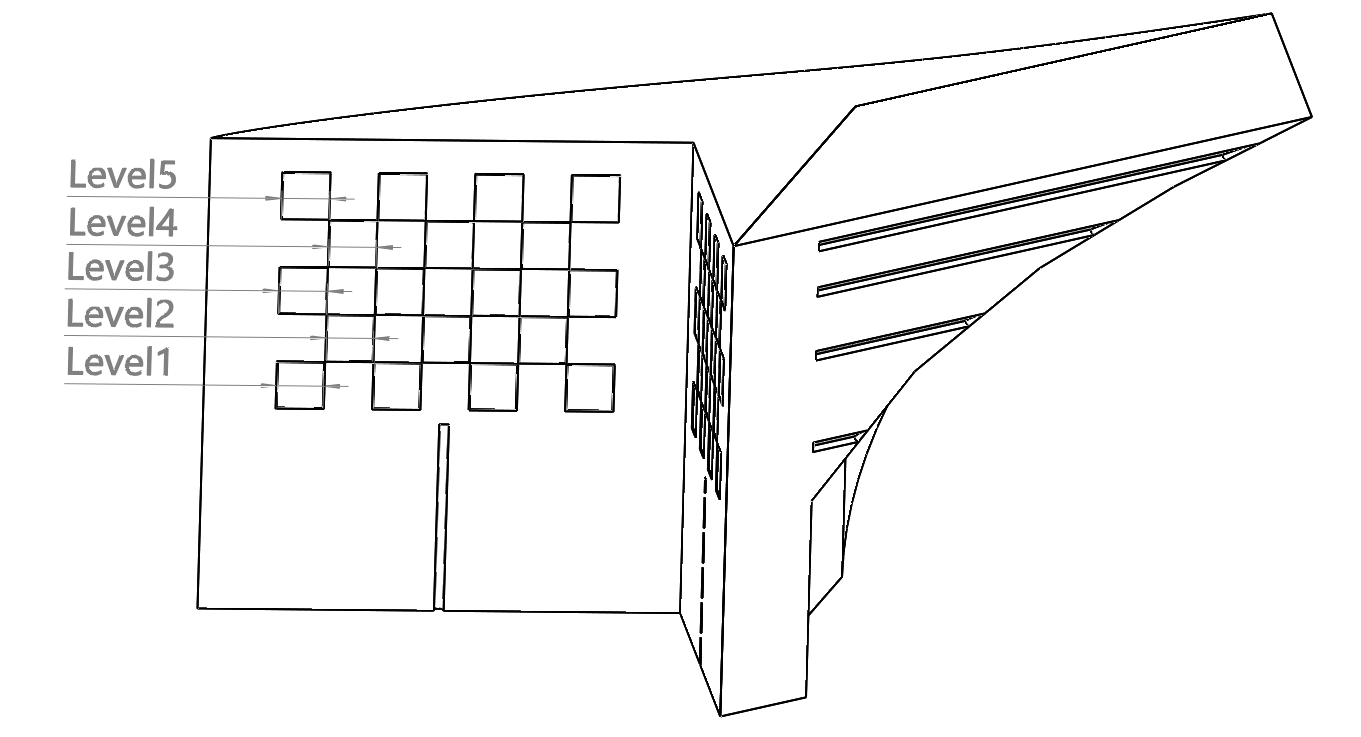
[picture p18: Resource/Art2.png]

Record the number of cameo level that is well printed.

Check the stringing

Check the ringing

## Overhang & Bridge

####
avatar

This is the front view of the test model.You should measure the minimum distance between the bridge and base. Check if the space under bridges are clear.
####
avatar

Check if there are major defects. Record the number of level that is perfectly printed.

# Example

# FAQs

# Score Weight

| Score Distribution | | | |
|---|---|---|---|
| section | subsection | Weight | Subtotal |
| Part1: Basic Precision | XY relative precision | 6 | 18 |
| | XY accuracy | 4 | |
| | Small Scale accuracy | 4 | |
| | Z axis accuracy | 4 | |
| Part2: Engineering | Base Quality | 10 | 25 |
| | Edge and corner | 5 | |
| | Large  Holes | 2\.5 | |
| | Large Shafts | 2\.5 | |
| | Small  Holes | 2\.5 | |
| | Small Shafts | 2\.5 | |
| Part3: Art | Overhang Level | 4 | 25 |
| | cameo level | 4 | |
| | Ringing size\(Included\) | 5 | |
| | Clear space between bridge | 1 | |
| | Bridge to bottom Distance\(mm\) | 3 | |
| | Stringing | 3 | |
| | Full height | 1 | |
| | Disk\(Minimum layer height\) | 4 | |
| Part4:Time | Engineering1 | 10 | 32 |
| | Engineering2 | 6 | |
| | Art1 | 10 | |
| | Art2 | 6 | |
| Total | 100 | | |

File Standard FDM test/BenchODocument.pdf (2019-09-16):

## OPERATION MANUAL

# BenchO In a nut shell

### Started by

### BetterPrint3r.Inc

### BenchO project group

### September 12, 2019

Abstract

BenchO is an open source project started by BetterPrint3r.Inc. Aiming to provide a uni-

versal test standard for the field. In the test, we provide specialised models and procedure to

estimate the capability of your 3D printer. The test now is for consumer grade FDM printer

only. The project is entirely open source. Suggestions and comments are always welcomed.

1

## Contents

1 Preparation for a standard test | 1
2 Take measurement | 5
3 Result Data analysis | 12
4 Acknowledgement | 16
5 Appendix | 17

BenchO in a nutshell | BenchO manual

## 1 Preparation for a standard test

### 1.1 Print models

General Info

In the following section we will specify the parameters for standard test. You should print 6 parts

in total to perform a complete test.

In our official test, all data are collected with standard PLA+ filament from eSUN.This type of

filament should be widely available and easy to purchase. If you use other types of filament. The

result will be less comparable and will not be accept for official ranking.

This standard is created for desktop FDM 3D printers. Using this on other types of printer will

generate inconclusive results.

About Slicing software

All models should strictly follow the designated parameters in a standard test. You should start with

a default profile in your slicing software and then change the parameters specified in the following

section. For the parameters undeclared in the following section, keep it default.

Turn on all possible settings in your slicer. If you cannot find the settings required. Then it must be

hidden in some advance menu in your slicing software.

Do not rotate the model along Z Axis in your slicing software

If you found severe issue with build plate adhesion, you can add brim. But we recommend you not to do so.

Basic precision

There is only one model in this section. Basic.stl

Using any default profile will be sufficient. You do not have to modify anything in specific but

you could try different layer height.

Engineering

There are two models: Engineering1.stl and Engineering2.stl

Table 1: Engineering1.stl

Setting | Parameter
Layer height | 0.2mm
Wall line count | 2
Infill density | 100%
Infill pattern | line
Support | None

Table 2: Engineering2.stl

Setting | Parameter
Layer height | 0.2mm
Wall line count | 2
Infill density | 66%
Infill pattern | Triangles
Top layers | 0
Bottom layers | 0
Support | None

Art

There are two models: Art1.stl and Art2.stl

Table 3: Art1.stl

Setting | Parameter
Layer height | 0.2mm
Wall line count | 3
Infill density | 0%
Top layers | 0
Support | None

Table 4: Art2.stl

Setting | Parameter
Layer height | 0.2mm
Wall line count | 2
Infill density | 20%
Support | None

Ruler

There are one model:Ruler.stl

Table 5: Ruler.stl

Setting | Parameter
Layer height | 0.2mm
Wall line count | 2
Infill density | 20%
Support | None

Ruler Placement


Figure 1: When printing this part you should put the ruler along one of the axis

### 1.2 Tools

A caliper with resolution not less than 0.01mm and range larger than 100mm will be sufficient for

the measurement. All data should be taken in metric system.

The printed ruler in previous section will be your additional tool.

Check your ruler with known straight edge.

## 2 Take measurement

### 2.1 Basic precision

During measurement you should ignore the defects that are easy to remove. The test is designed to

reflect the capability of your printer.

Large Scale


Figure 2: This is the top view of the test model.You should take 8 measurements and fill the associative blank.

Small Scale


Figure 3: This is the top view of the test model.You should take 10 measurements and fill the associative blank.In this part you do not have to take data by order.

Z Axis


Figure 4: This is the front view of the test model.You should take 4 measurements and fill the associative blank.In this part you do not have to take data by order.

### 2.2 Engineering

Surface flatness and parallel

Horizontal thickness


Figure 5: You should take 8 measurements and fill the associative blank.

Vertical thickness


Figure 6: You should take 6 measurements and fill the associative blank.

Curvature

You should first bolt or fix your ruler in one of the four corner and then measure the gap between

your ruler and the opposite side of the base. If there is no gap at all. Your result will be 0mm.

Curvature X Axis


Figure 7: This will be an example for X axis measure

Curvature Y Axis


Figure 8: This will be an example for Y axis measure

Shafts and holes

Shafts and holes


Figure 9: This is the Top view of the test model.You should take 6 measurements for each dimension and fill the associative blank.

### 2.3 Art

Bridge


Figure 10: This is the front view of the test model.You should measure the minimum distance between the bridge and base. Assess the degree of stringing between spikes.

Overhang


Figure 11: Check if there are major defects. Record the number of level that is perfectly printed.

Cameo and Ringing


Figure 12: Record the number of cameo level that is well printed.

## 3 Result Data analysis

### 3.1 Basic precision

The aim of this part is to characterise the basic properties of your printer. The difference between

designed and printed is called accuracy. And the distribution (relative difference from average) is

called precision.

For all accuracy assessment we applied ISO 286. We took the maximum difference from the

designed and see which tolerance grade it fits in. The maximum score for accuracy is 4.See Ap-

pendix for more detailed information.

For precision measurement we use a classic natural log function:

Score = 6e

−σ
(1)

Where σ is the standard deviation calculated from collected data. With formula:

σ =

s
∑

N
i=1

(x−x¯i)

2
N −1

(2)

Where N is the total number of data collected.

### 3.2 Engineering

This part refers to model Engineering1.stl. The model is actually an nema 17 step motor base.

By printing this 100 % infill part we would evaluate the capability of your printer to produce

engineering part that needs to be solid and accurate.

Section1:Flatness and Parallel

There are 9 measurement for thickness (T1-T9). Where the last one is the middle point thickness.

The degree of Parallel is determined by the difference of averages values between opposite side.

The divergence in this section reflects the angle between your upper edge direction and your lower

edge ones.

For example, in figure 5 the X direction divergence will be calculated by:

Div = Sin⁻1(

T1+T2+T3
T5+T6+T7
) | (3)

The base surface is marked as uneven if either the standard deviation of the thickness is larger than

0.5 or the maximum difference between data is larger than 0.4. If the surface is Uneven then the

flatness score will be halved:
i f Uneven A = 0.5

else A = 1

(4)

The other part of flatness will be measured by the standard deviation σT for all thickness point:

Score = Ae⁻σT
(5)

These two values are multiplied to produce the final flatness score.

Section1:Vertical distortion

In this section we measure the degree of overshooting due to motor movement. If the machine

cannot properly accelerate and decelerate then it will leave a relative large difference between point

V1,V6 and the rest.

The score it calculated by fitting the maximum distortion in to our tolerance table.

Section2:Curvature

This section shows the curvature and bending of your printed base part (which is the base of

Engineering1.stl). The radius in this section calculated by using the bottom base edge as the

arc of a circle. For an ideal plane the radius should be infinite.

The approximate radius is calculated by:

r =

L
2sin(tan⁻¹(

d
L

))

(6)

Where L is the length of the base and d is the mean bending distance you obtained.And the score

is then calculated by:

score = 1−e

−

r
103.5 | (7)

Section3:Shafts and Holes

In this section the ability to print holes and shafts are tested. For each dimension (Large inner,Large

outer, etc) two main features are valued. First is the relative precision of the holes or shafts printed.

The difference of extremes are fitted in to H/h grades in ISO 286-2 chart. The difference between

actual printed holes/shafts and designed ones is compared with ISO 286 Chart. Which will be

valued the same as it is in basic precision. Additionally, if a hole is undersized or a shaft is over-

sized. The deduction of marks will be doubled. This is because in real life an oversized shaft and a

undersized hole will be really painful to fit.

### 3.3 Art

In art we evaluate the ability of your printer to produce artistic products.

A printer with good score in stringing and ringing test will do better in producing good surface

detail.

Cameo level, disk feature and spikes tells you how well your printer is in making fine details

and small structures.

The overhang and bridge test shows the cooling ability of your print head.

A printer score high in art section will likely to produce art with fewer defects.

## 4 Acknowledgement

### 4.1 License

Apache 2.0 (http://www.apache.org/licenses/LICENSE-2.0) is applied in BenchO project.

## 5 Appendix

### 5.1 Tolerance Table (ISO 286)

Tolorence table

Grade 100mm(mm) 10mm(mm) 30mm(mm) 50mm(mm) 80mm(mm) Score

Perfect | 0.000 | 0.000 | 0.000 | 0.000 | 0.000 | 1.00
IT8 | 0.054 | 0.022 | 0.033 | 0.039 | 0.046 | 1.00
IT9 | 0.087 | 0.036 | 0.052 | 0.062 | 0.074 | 0.90
IT10 | 0.140 | 0.058 | 0.084 | 0.100 | 0.120 | 0.80
IT11 | 0.220 | 0.090 | 0.130 | 0.160 | 0.190 | 0.70
IT12 | 0.350 | 0.150 | 0.210 | 0.250 | 0.300 | 0.60
IT13 | 0.540 | 0.220 | 0.330 | 0.390 | 0.460 | 0.50
IT14 | 0.870 | 0.360 | 0.520 | 0.620 | 0.740 | 0.40
IT15 | 1.400 | 0.580 | 0.840 | 1.000 | 1.200 | 0.30
IT16 | 2.200 | 0.900 | 1.300 | 1.600 | 1.900 | 0.10
Reject | 3.000 | 3.000 | 3.000 | 3.000 | 3.000 | 0.00

### 5.2 Shafts and Holes (ISO 286-2)

Shafts

Grade (30mm,50mm] (50mm,80mm] (80mm,120mm] Score

Perfect | 0.000 | 0.000 | 0.000 | 1.00
5 | 0.011 | 0.001 | 0.015 | 1.00
6 | 0.016 | 0.019 | 0.022 | 0.90
7 | 0.025 | 0.030 | 0.035 | 0.80
8 | 0.039 | 0.046 | 0.054 | 0.70
9 | 0.062 | 0.074 | 0.087 | 0.60
10 | 0.100 | 0.120 | 0.140 | 0.50
11 | 0.160 | 0.190 | 0.220 | 0.30
12 | 0.250 | 0.300 | 0.350 | 0.10
Reject | 1.000 | 1.000 | 1.000 | 0.00

Holes

Grade <=30 <=50 <=80 <=120 Score

Perfect 0.000 0.000 0.000 0.000 | 1.00
6 | 0.013 0.016 0.019 0.022 | 1.00
7 | 0.021 0.025 0.030 0.035 | 0.90
8 | 0.033 0.039 0.046 0.054 | 0.8
9 | 0.052 0.062 0.074 0.087 | 0.6
10 | 0.084 | 0.1 | 0.12 | 0.14 | 0.4
11 | 0.13 | 0.16 | 0.19 | 0.22 | 0.2
Reject | 1.00 | 1.00 | 1.00 | 1.00 | 0.00

### 5.3 Art

Cameo level

level | Score
0 | 0.00
1 | 0.20
2 | 0.40
3 | 0.60
4 | 0.80
5 | 1.00

Stringing level

Condition Score

Clean | 1.00
Ok | 0.60
Bad | 0.20
Fail | 0.00

Spikes

Height | Score
Full | 1.00
Most | 0.70
Some | 0.50
Nope | 0.00

Disk

Height Score

0.025mm 1.00

0.05mm | 0.70
0.1mm | 0.50
Fail | 0.00

Overhang

Height | Score
4 | 1.00
3 | 0.75
2 | 0.50
1 | 0.25
0 | 0.00

Ringing level

Condition Score

2mm | 1.00
4mm | 0.70
8mm | 0.50
Fail | 0.00

### 5.4 Score Weight

section | subsection | Weight Subtotal
Part1: Basic Precision | XY relative precision | 6
| | 18
| XY accuracy | 4
| Small Scale accuracy | 4
| Z axis accuracy | 4
Part2: Engineering | Base Quality | 10

25

| Edge and corner | 5
| Large Holes | 2.5
| Large Shafts | 2.5
| Small Holes | 2.5
| Small Shafts | 2.5
Part3: Art | Overhang Level | 4

25

| cameo level | 4
| Ringing size(Included) | 5
| Clear space between bridge | 1
| Bridge to bottom Distance(mm) | 3
| Stringing | 3
| Full height | 1
| Disk(Minimum layer height) | 4
Part4:Time | Engineering1 | 10

32

Engineering2 | 6
Art1 | 10
Art2 | 6
Total | 100

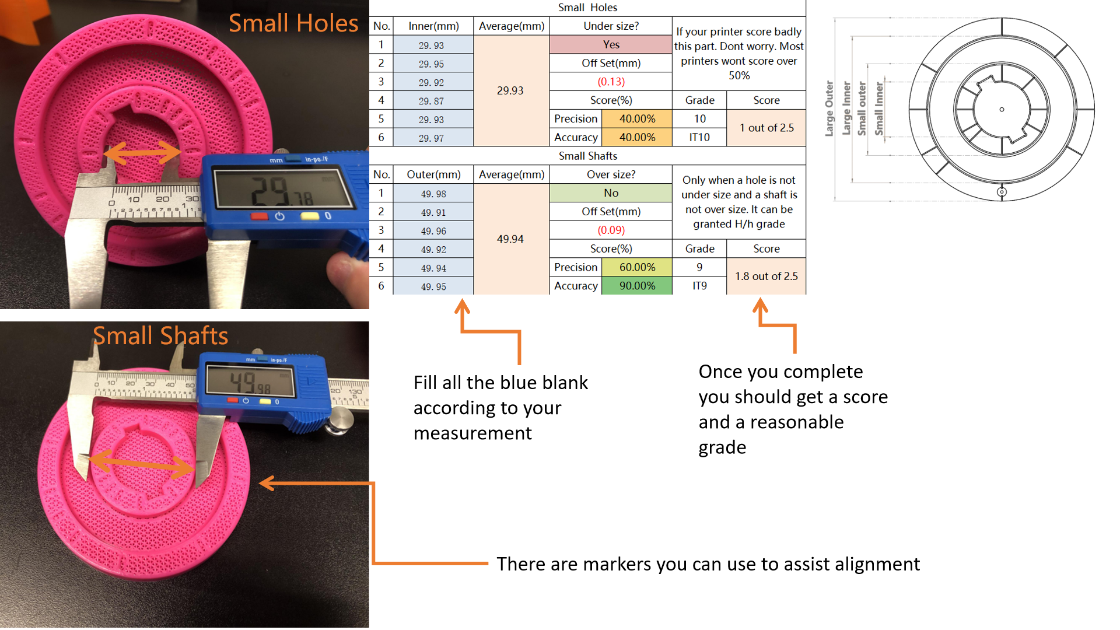
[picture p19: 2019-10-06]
Standard FDM test/Example/eng2_example2.png

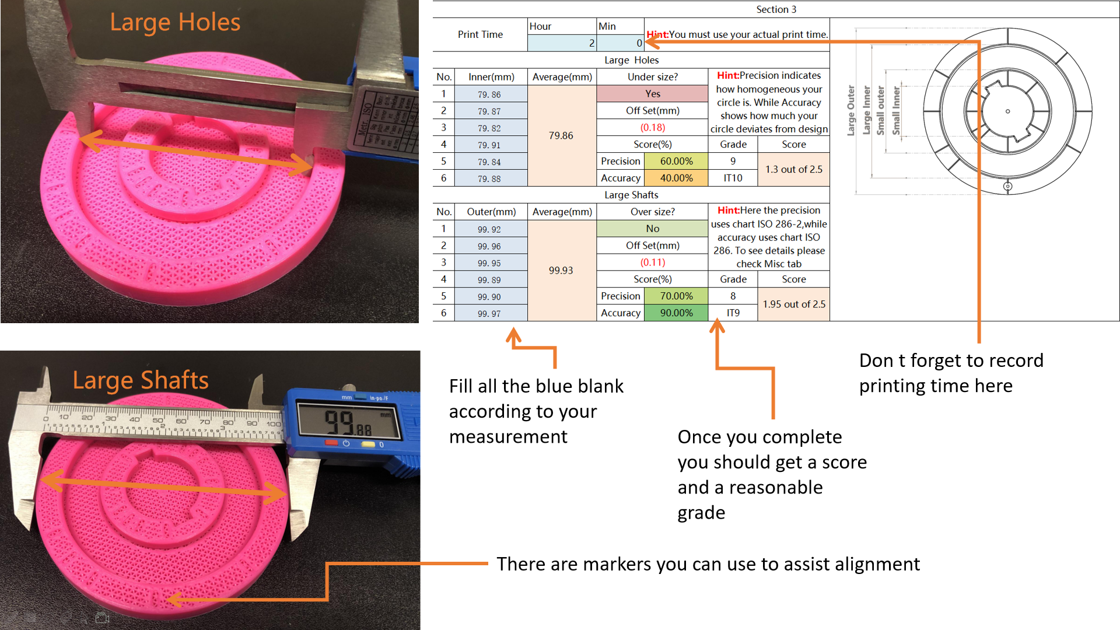
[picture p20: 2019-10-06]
Standard FDM test/Example/eng2_example1.png

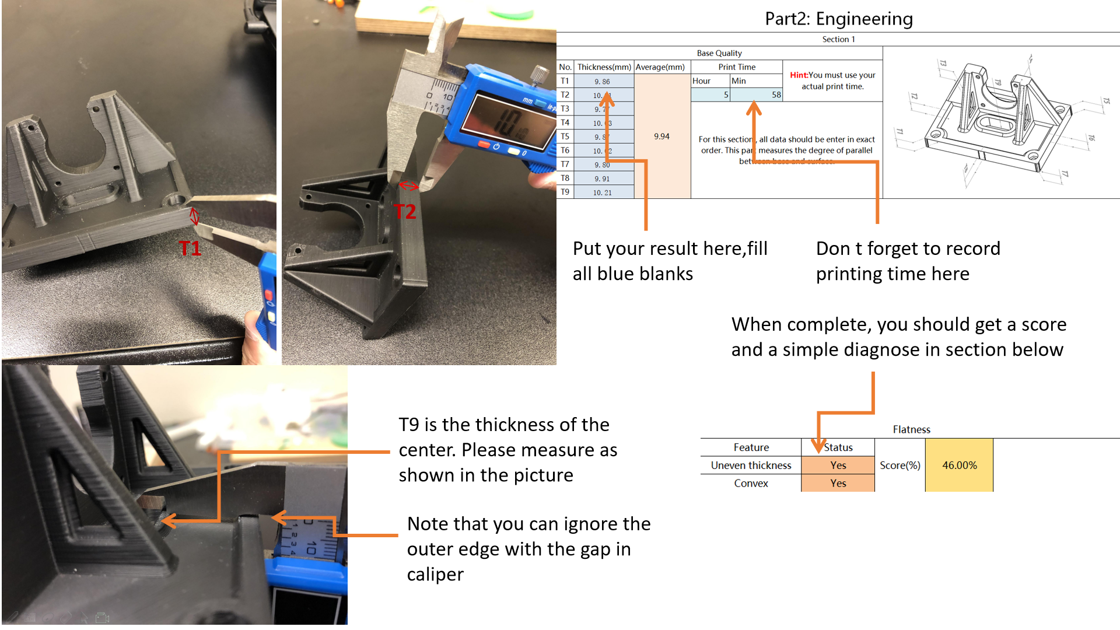
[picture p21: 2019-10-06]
Standard FDM test/Example/eng1_example1.png

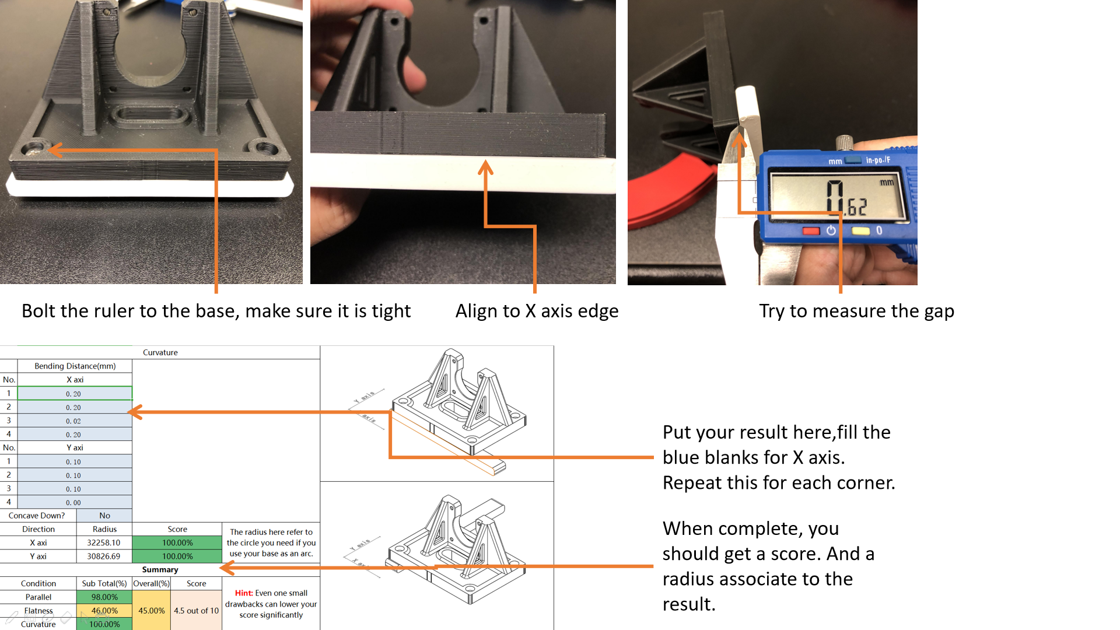
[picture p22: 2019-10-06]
Standard FDM test/Example/eng1_example3.png

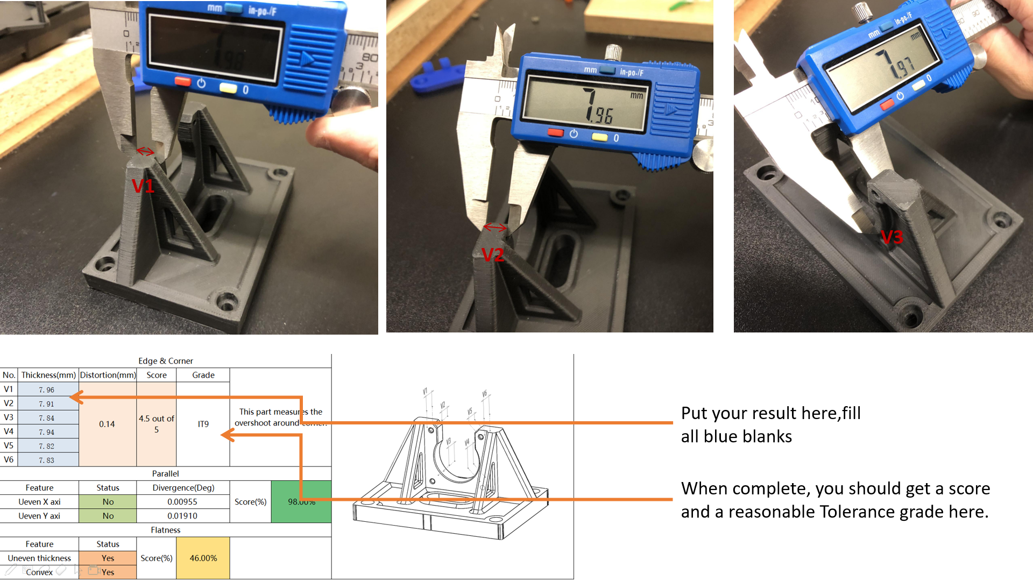
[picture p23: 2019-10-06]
Standard FDM test/Example/eng1_example2.png

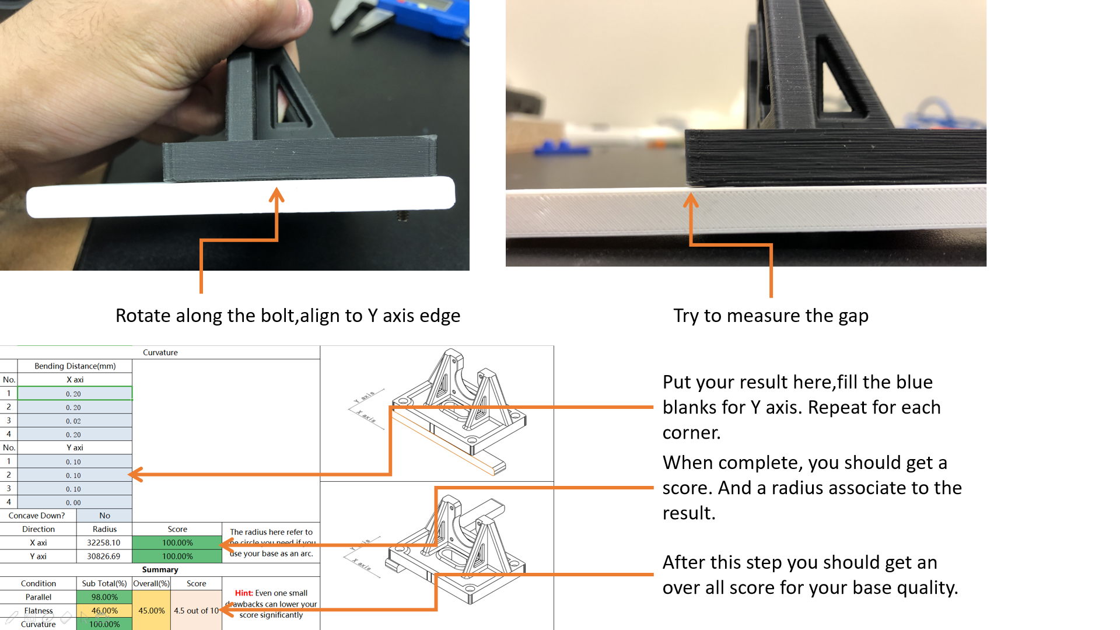
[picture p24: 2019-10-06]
Standard FDM test/Example/eng1_example4.png
